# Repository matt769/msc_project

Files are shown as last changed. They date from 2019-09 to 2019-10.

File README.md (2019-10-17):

### Code
Need to run cmake/make in each of the subfolders except Microcontroller which contains Arduino/Teensyduino code files.  
FullRobot should be done last.  

Host code:  
* maps  
* path_planning  
* communication  
* FullRobot  

Microntroller code:  
* Microcontroller/Robot
* Microcontroller/IMU_calibration
* Microcontroller/Rotation

Host code dependencies:
* https://github.com/matt769/ORB_SLAM2_PRJ - clone this into same directory as this repository
* Eigen
* OpenCV
* Pangolin
* FlyCapture API (if installed in other than its default location then may need to modify FullRobot/CMakeLists.txt)

Microcontroller code dependencies (see report for links):
* PU9250
* PWMServo
* PID_v1
* Rotation (files provided, but need to be placed in stardard Arduino library location)

Other
* May need to modify include path in Robot.ino to point to communication/commPackages.h

### Supporting materials
See the Supporting_materials folder for:  
- Odroid setup instructions
- Robot build notes
- Robot development state notes *TO ADD*
- 3D/2D design files

See this link https://www.dropbox.com/sh/bz3t7idnc23njo4/AABDjr6x9dCKdW70Yl40RJT0a?dl=0 for:  
- FlyCapture API files
- Component datasheets
- Point cloud maps *TO ADD*

See this link https://github.com/matt769/2017-10_Transmitter_v2 for:
- Transmitter code

### To run
 More details on the connections are available in `build notes.pdf` if required. This is just a quick summary.

#### Using Odroid as the main computer
 * Connect Odroid and camera
 * Connect the switches and battery connectors
 * Turn them both on (Odroid circuit can be left off if just radio controlling the vehicle)
 * Connect to Odroid via ethernet cable
 * Open SSH session: IP 169.254.130.11, Username: odroid, Password: odroid
 * Run:
   * $ cd ~/ws/project/FullRobot
   * $ ./full ../../ORB_SLAM2_PRJ/Vocabulary/ORBvoc.txt PGchameleon_lowres.yaml n

#### Using an external computer
 * Connect external computer and camera
 * Connect the switch for the low level circuitry only (i.e. not the Odroid)
 * Turn it on
 * On the external computer, assuming it has the same folder structure as the Odroid (but easy to modify if not), run:
   * $ cd ~/ws/project/FullRobot
   * $ ./full ../../ORB_SLAM2_PRJ/Vocabulary/ORBvoc.txt PGchameleon_lowres.yaml y

#### Notes
The program `full` takes 3 parameters.
1. Path to Bag of Words Vocabulary file
2. Path to ORB SLAM config file (including camera intrinsic parameters) 
3. Visualisation indicator - `y` will launch the standard ORB SLAM windows to view the camera feed and map/localisation information, `n` will suppress then

In the above running instructions I have assumed visualisation disabled when using Odroid, and enabled when using an external computer.

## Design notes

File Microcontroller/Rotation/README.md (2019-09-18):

# Rotation
Library for working with 3D rotations and orientations.
Mainly written for use of quaternions. Basic Euler and and Vector objects added to support.

For Euler angles, the rotation order used is always YAW -> PITCH -> ROLL.

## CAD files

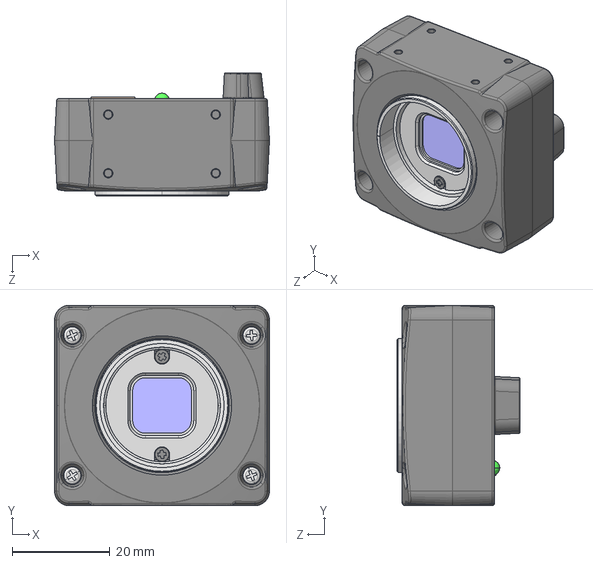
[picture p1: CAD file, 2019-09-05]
Supporting_materials/Datasheets/Camera/Drawings/Chameleon Case.STEP
44.0 x 41.0 x 25.2 mm

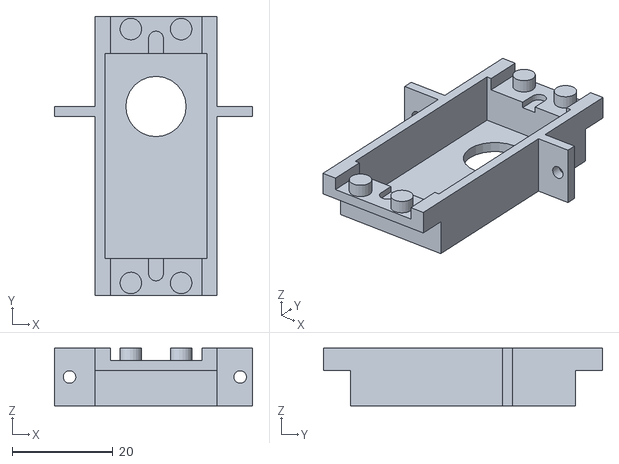
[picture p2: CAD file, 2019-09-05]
Supporting_materials/Design_files/for_3d_printing_pt2.stl
39.4 x 55.5 x 11.5

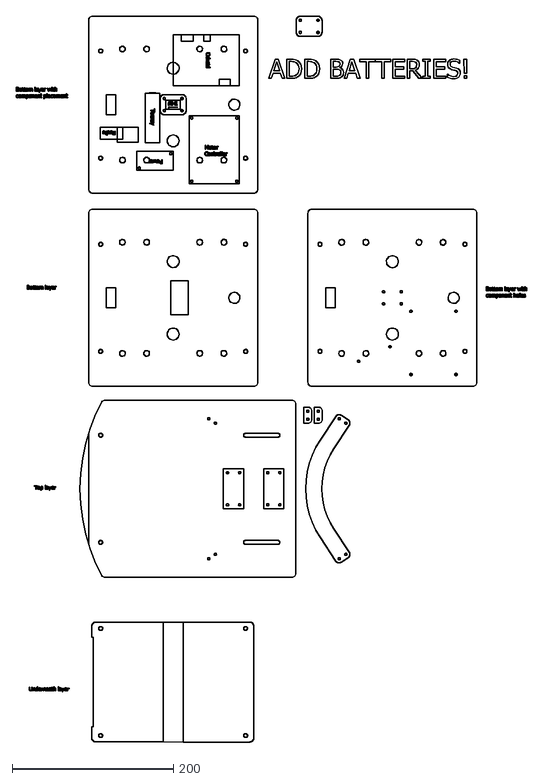
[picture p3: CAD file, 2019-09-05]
Supporting_materials/Design_files/layers_and_components.dxf
634.1 x 901.6

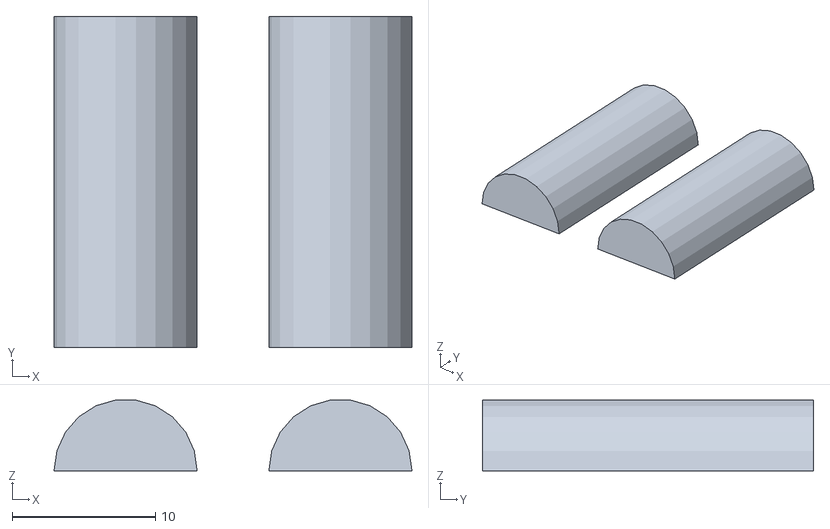
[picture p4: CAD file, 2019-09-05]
Supporting_materials/Design_files/for_3d_printing_pt4.stl
25.0 x 23.1 x 4.95

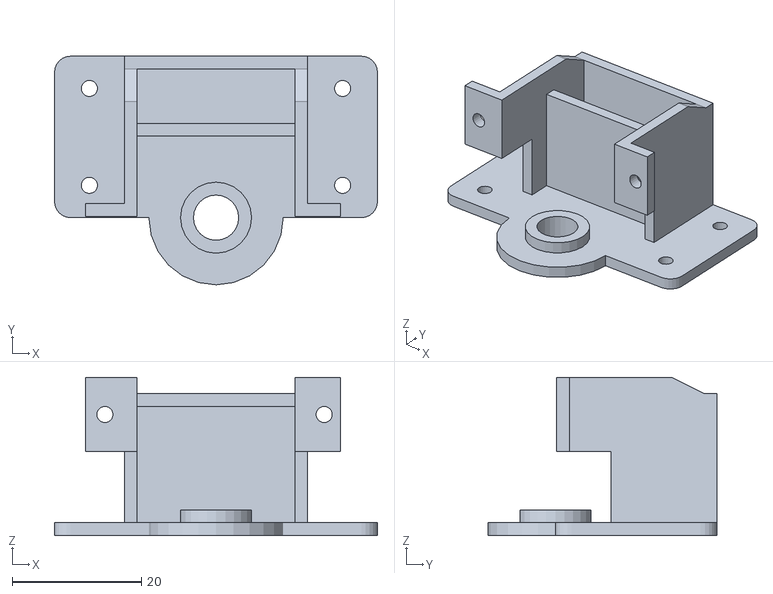
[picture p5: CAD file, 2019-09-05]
Supporting_materials/Design_files/for_3d_printing_pt1.stl
50.0 x 35.4 x 24.5

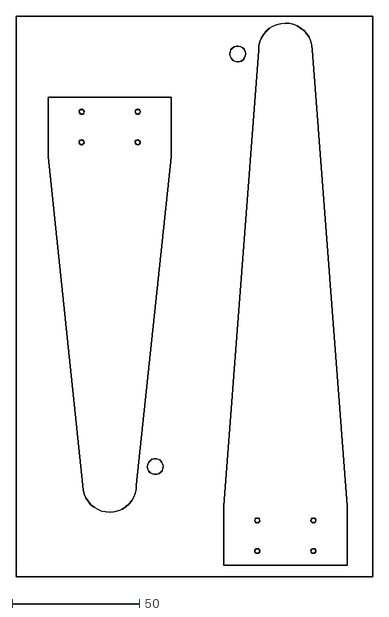
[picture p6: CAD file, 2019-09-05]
Supporting_materials/Design_files/camera_lever_for_laser_cutting.dxf
140.0 x 220.0

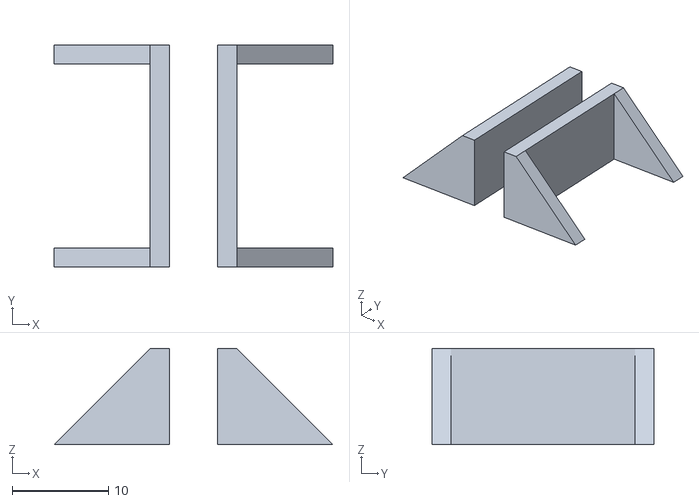
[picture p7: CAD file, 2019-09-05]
Supporting_materials/Design_files/for_3d_printing_pt3.stl
29.0 x 23.1 x 10.0

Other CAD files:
Supporting_materials/Datasheets/Camera/Drawings/Chameleon Case.x_b

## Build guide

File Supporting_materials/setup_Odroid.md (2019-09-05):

# Setting up the Odroid XU4

## Initial setup

Download Ubuntu 18.04 image for Odroid from here:  
https://wiki.odroid.com/odroid-xu4/os_images/linux/ubuntu_4.14/ubuntu_4.14  
And put on SD or eMMC card for Odroid  

Power on Odroid  
It will shut down automatically if this is the first time it's been turned on  
Turn it on again  

Now when it restarts, update linux  
$ sudo apt update  
$ sudo apt upgrade  

I received an error:  
"depmod ... module not found"  
-> according to forum this is not a problem https://forum.odroid.com/viewtopic.php?t=33481

$ sudo apt dist-upgrade
$ sudo apt autoremove
$ sudo apt install linux-image-xu3

I received an error:  
"unable to locate package"  
-> apparently not a problem, the previously dist-upgrade step should have been sufficient https://forum.odroid.com/viewtopic.php?t=31484

## Tools and dependencies
Create workspace directory  
$ mkdir ws  

### Git
$ sudo apt install git

### Eigen
$ sudo apt-get install libeigen3-dev

Note: I previously installed Eigen using the Github hosted source, but later had problems with g2o finding it

### OpenCV
$ cd ~/ws
$ sudo apt-get install cmake git libgtk2.0-dev pkg-config libavcodec-dev libavformat-dev libswscale-dev  
$ wget https://github.com/opencv/opencv/archive/3.4.2.zip  
$ unzip 3.4.2.zip  
$ cd ~/opencv  
$ mkdir build  
$ cd build  
$ cmake -D CMAKE_BUILD_TYPE=Release -D CMAKE_INSTALL_PREFIX=/usr/local ..  
$ make -j4  
$ sudo make install  

Note: I was not able to get OpenCV to install with Eigin (couldn't get it to find Eigen properly), though this is not actually required

### Pangolin
$ cd ~/ws
$ git clone https://github.com/stevenlovegrove/Pangolin.git  
$ sudo apt-get install libglew-dev  
$ cd Pangolin  
$ mkdir build  
$ cd build  
$ cmake ..  
$ cmake --build .  

### ORB_SLAM2_PRJ
$ git clone https://github.com/matt769/ORB_SLAM2_PRJ  
$ cd ORB_SLAM2_PRJ  
$ ./build.sh  

Note: The build.sh file is modified to include the -j2 argument for make when building ORB SLAM. Without this the ORB SLAM build will probably fail (on the Odroid) due to memory issues (though g2o and DBoW2 should be ok). For systems with more memory, this can be changed back to -j.

### FlyCapture
See this page:  
https://www.flir.co.uk/support-center/iis/machine-vision/application-note/getting-started-with-flycapture-2-and-arm/

I have put the file on dropbox
$ cd ~/ws
$ wget https://www.dropbox.com/s/503t7ibigvr35u0/flycapture.2.13.3.31_armhf_xenial.tar.gz?dl=0
$ mv flycapture.2.13.3.31_armhf_xenial.tar.gz?dl=0 flycapture.2.13.3.31_armhf_xenial.tar.gz
$ tar -xzf flycapture.2.13.3.31_armhf_xenial.tar.gz

$ cd flycapture.2.13.3.31_armhf/lib  
$ sudo cp libflycapture* /usr/lib  
$ sudo sh flycap2-conf  
I used user name "odroid"  
$ cd src/FlyCapture2Test  
$ make  

## Networking
Ubuntu 18.04 uses a new system (not interfaces file anymore)  

Place fillowing file 'config.yaml' (actual name doesn't matter) in /etc/netplan/  
</pre>
network:  
  version: 2  
  renderer: networkd  
  ethernets:  
    enp3s0:  
      addresses:  
        - 169.254.130.11/24  
</pre>

## Serial port permissions
This gives read/write permissions on ttyACM0  

$ sudo adduser odroid dialout  

Actually the odroid user is already a member of the dialout group. This is not the case with a standard Ubuntu install (e.g. on a laptop) I think.

## Teensy rules

Download the device rules from here https://www.pjrc.com/teensy/td_download.html
$ sudo cp 49-teensy.rules /etc/udev/rules.d/

## For normal computer
Process will be basically the same, but ensure that the correct version of the FlyCapture software is installed e.g. AMD64 for my laptop.

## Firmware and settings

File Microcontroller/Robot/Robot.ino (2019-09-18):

#include <Arduino.h>
#include <avr/io.h>
#include <avr/interrupt.h>

#include "Receiver.h"
#include "Motors.h"
#include "MPU9250.h"
#include <PWMServo.h>
#include <PID_v1.h>
#include "/home/matt/ws/project/communication/commPackages.h"
#include <Rotation.h>
#include"movingAverageFilter.h"


using namespace Comms;

uint8_t sendPackageId = 0;

// STATUS - note this is currently part of Comms, maybe should change that
Status status = Status::UNINITIALISED;
Status statusPrev = Status::UNINITIALISED;
constexpr uint8_t pinLED = 13;

MoveStatus moveStatus = MoveStatus::FINISHED;
MoveStatus moveStatusPrev = MoveStatus::FINISHED;
namespace MoveStatusDetail {
enum Enum {
  NONE,
  TURN,
  FORWARD,
  ARC
};
}
MoveStatusDetail::Enum moveStatusDetail = MoveStatusDetail::NONE;



// MODE
namespace Mode {
enum Enum {
  MANUAL,
  AUTO
};
}
Mode::Enum mode = Mode::AUTO;
Mode::Enum modePrev = Mode::AUTO;

namespace TurnDirection {
enum Enum {
  NONE,
  LEFT,
  RIGHT
};
}
TurnDirection::Enum turnDirection = TurnDirection::NONE;

namespace RobotDirection {
enum Enum {
  FORWARD,
  BACKWARD
};
}
RobotDirection::Enum robotDirection = RobotDirection::FORWARD;


// For communication with Odroid
constexpr uint8_t rxBufferSize = 32;
char rxBuffer[rxBufferSize]; // TODO review size

MovePackageRequest movePackageRequest;
PosePackageRequest posePackageRequest;
ServoPackageRequest servoPackageRequest;
StatusPackageRequest statusPackageRequest;

PackageType packageType = PackageType::EXAMPLE0;
bool newMoveRequest(false), newPoseRequest(false), newServoRequest(false), newStatusRequest(false);

constexpr uint32_t moveUpdatePeriod = 500; // how often during a movement phase that the robot will send an update to the host with distance so far



// Motors
constexpr uint8_t pinDir1 = 38;
constexpr uint8_t pinPwm1 = 37;
constexpr uint8_t pinDir2 = 36;
constexpr uint8_t pinPwm2 = 35;

Motor motorLeft(pinDir1, pinPwm1);
Motor motorRight(pinDir2, pinPwm2);
uint8_t throttleLeft;
uint8_t throttleRight;

constexpr uint8_t LOW_THROTTLE_LIMIT = 30;
constexpr uint8_t STICK_DEADZONE = 8; // on either side of centre
constexpr uint8_t STICK_CENTRE = 127;
constexpr uint8_t THROTTLE_MAX = 250;

// Servo
constexpr uint8_t pinServo = 30;
PWMServo camServo;
constexpr int servoPositionCentre = 85;
int servoPosition = servoPositionCentre; // offset + 0 // note that position is relative to centred position
constexpr int SERVO_POS_MIN = servoPositionCentre - 35; // to the left
constexpr int SERVO_POS_MAX = servoPositionCentre + 35; // to the right


// Receiver
constexpr uint8_t pinRadioCE = 25;  // RF24 enable
constexpr uint8_t pinRadioCSN = 26; // SPI Chip Select
Receiver receiver(pinRadioCE, pinRadioCSN);
uint32_t receiverLast = 0;
constexpr uint32_t receiverFreq = 50;
bool newRxData;
bool radioArmed = false;

// Encoders
constexpr uint8_t pinEncoderIntL = 18; // S1 (orange)
constexpr uint8_t pinEncoderOtherL = 17; // S2 (green)
constexpr uint8_t pinEncoderIntR = 16; // S1 (orange)
constexpr uint8_t pinEncoderOtherR = 15; // S2 (green)
volatile int32_t encCountLeft = 0;
volatile int32_t encCountRight = 0;

float trackSpeedLeft;
float trackSpeedRight;


// PIDs
// Track speeds are in millimetres per second
uint32_t lastCalculateSpeeds = 0;
constexpr uint32_t pidPeriodSpeeds = 20; // milliseconds (e.g. 20ms -> 1000/20 = 50Hz)

float leftTrackSpeedSetpoint = 0, leftTrackSpeedOutput;
float rightTrackSpeedSetpoint = 0, rightTrackSpeedOutput;
float leftKp = 0.1, leftKi = 0, leftKd = 0;
float rightKp = 0.1, rightKi = 0, rightKd = 0;

PID pidLeftTrackSpeed(&trackSpeedLeft, &leftTrackSpeedOutput, &leftTrackSpeedSetpoint, leftKp, leftKi, leftKd, PID_DIRECT);
PID pidRightTrackSpeed(&trackSpeedRight, &rightTrackSpeedOutput, &rightTrackSpeedSetpoint, rightKp, rightKi, rightKd, PID_DIRECT);



uint32_t lastCalculateHeading = 0;
constexpr uint32_t pidPeriodHeading = 100; // milliseconds

float heading = 0, requiredAngularVelocity = 0, headingSetpoint = 0;
float zeroHeading = 0;
float headingError = 0; // This will be used along with a setpoint of zero instead of the actual heading and setpoint
//  as it allows easier control of the heading wrapping
float headingKp = 2, headingKi = 0, headingKd = 0;
PID pidHeading(&headingError, &requiredAngularVelocity, &zeroHeading, headingKp, headingKi, headingKd, PID_DIRECT);




// Track movement
Vector position(0, 0, 0);


// Note, turn target is headingSetpoint so no separate variable created
float forwardTarget = 0.0;
float forwardActual = 0.0;

constexpr float headingTolerance = 5.0 * PI / 180.0;
constexpr float forwardTolerance = 5.0; // millimetres

uint32_t lastAccumulate;
constexpr uint32_t accumulatePeriod = 5;
uint32_t lastHandleMovement;
constexpr uint32_t handleMovementPeriod = 20;



// Robot measurements
constexpr int32_t driveSprocketRadius = 21;
constexpr float driveSprocketCircumference = 2.0 * PI * (float)driveSprocketRadius;
constexpr int32_t pulsesPerMotorRotation = 2;
constexpr int32_t gearRatio = 75;
constexpr float distancePerPulse = driveSprocketCircumference / (float)(pulsesPerMotorRotation * gearRatio);
constexpr float distanceBetweenTracks = 211.0;


// IMU
MPU9250 IMU(SPI1, 4);
int imuStatus;

unsigned long readImuLast = 0;
constexpr unsigned long readImuPeriod = 2; // milliseconds, e.g. 2ms = 500Hz
constexpr float readImuPeriodFloat = (float)readImuPeriod / 1000.0; // convert to seconds
Euler eulerAngles;
Quaternion orientation(1, 0, 0, 0);
float alpha = 0.01; // weight of accel in complementary filter

movingAverageFilter magXfilter;
movingAverageFilter magYfilter;
movingAverageFilter magZfilter;






// INTERRUPTS
// Because the interrutps are set to trigger on CHANGE we need to find out whether it was rising or falling
// So just read the pin again, if it's high, then it was rising
// And in one direction, both pins will be the same level, and in the other they'll be the opposite
void incrementCounterL() {
  if (digitalReadFast(pinEncoderIntL) == digitalReadFast(pinEncoderOtherL)) {
    encCountLeft += 1;
  }
  else {
    encCountLeft -= 1;
  }
}

void incrementCounterR() {
  if (digitalReadFast(pinEncoderIntR) != digitalReadFast(pinEncoderOtherR)) {
    encCountRight += 1;
  }
  else {
    encCountRight -= 1;
  }
}


// **************************************************************************************
// ************************************  SETUP  *****************************************
// **************************************************************************************

void setup() {
  //delay(2000); // required so we don't miss the first serial prints
  //while (!Serial); // This is required for the Teensy to get set up properly as a serial port on Linux
  // TODO ideally we should be able to start up with just the radio

  statusPrev = status;
  status = Status::INITIALISING;
  pinMode(pinLED, OUTPUT);
  digitalWrite(pinLED, HIGH);

  // Radio alternative SPI pins
  SPI.setSCK(27);

  // IMU alternative SPI pins
  SPI1.setSCK(20);
  SPI1.setMISO(5);
  SPI1.setMOSI(21);

  // Radio setup
  receiver.setup(); // TODO add check and halt program like IMU if required
  receiver.setAckBattery(7); // report full battery (to stop controller battery light flashing a lot)

  // if there's no serial connection but we do have radio input, then continue
  while ((!Serial) && (!receiver.checkForNewData())) {
    delay(100);
  }


  // Encoder setup
  setupEncoders();

  // IMU setup
  imuStatus = IMU.begin();
  if (imuStatus < 0) {
    Serial.println("IMU initialization unsuccessful");
    Serial.println("Check IMU wiring or try cycling power");
    Serial.print("Status: ");
    Serial.println(imuStatus);
    while (1) {} // TODO change to set status and error flags
  }

  // Specific settings
  // Some of these are already the default but for clarity I put them here anyway
  IMU.setAccelRange(MPU9250::ACCEL_RANGE_2G);
  IMU.setGyroRange(MPU9250::GYRO_RANGE_250DPS);
  IMU.setDlpfBandwidth(MPU9250::DLPF_BANDWIDTH_20HZ);
  // There aren't really any options available for Mag
  // Except read rate which is already set to 100Hz within IMU.begin()

  // calibration info
  IMU.setAccelCalX(0.2534242, 0.9977166);
  IMU.setAccelCalY(0.2825031, 0.9991337);
  IMU.setAccelCalZ(0.5199513, 0.9813061);

  IMU.setMagCalX(52.7316322, 0.8228859);
  IMU.setMagCalY(-36.4627380, 1.1055350);
  IMU.setMagCalZ(-24.8827744, 1.1360730);

  // initialise magmetometer filters
  initialiseMagFilters();
  // use accel and mag to get initial orientation
  calculateInitialOrientation();



  // Servo setup
  camServo.write(servoPosition);
  camServo.attach(pinServo);
  camServo.write(servoPosition);

  // wait for the expected radio input (throttle down-up-dowm) and then start main program
  //  receiver.armingProcedure();/
  motorLeft.setDir(MotorDirection::FORWARD);
  motorRight.setDir(MotorDirection::FORWARD);

  // PIDs
  pidLeftTrackSpeed.SetSampleTime(pidPeriodSpeeds);
  pidRightTrackSpeed.SetSampleTime(pidPeriodSpeeds);
  pidLeftTrackSpeed.SetOutputLimits(-30, 30);   // PWM
  pidRightTrackSpeed.SetOutputLimits(-30, 30);   // PWM
  pidLeftTrackSpeed.SetMode(PID_AUTOMATIC); // TODO after testing this should be removed - PID should only be on when a movement is being made
  pidRightTrackSpeed.SetMode(PID_AUTOMATIC); // TODO after testing this should be removed - PID should only be on when a movement is being made

  pidHeading.SetSampleTime(pidPeriodHeading);
  pidHeading.SetOutputLimits(-1, 1);  // Radians
  pidHeading.SetMode(PID_AUTOMATIC);


  // initialise all timing variables
  uint32_t timeNow = millis();
  lastCalculateSpeeds = timeNow;
  lastAccumulate = timeNow;
  lastHandleMovement = timeNow;
  readImuLast = timeNow;


  statusPrev = status;
  status = Status::READY;

  digitalWrite(pinLED, LOW);
  Serial.println(F("Starting..."));

  // FOR TESTING
  //  statusPrev = status;
  //  status = Status::ACTIVE;
}


// **************************************************************************************
// ************************************  LOOP  ******************************************
// **************************************************************************************

void loop() {

  receiveRequests();
  processStatusRequest(); // ALWAYS respond to status request

  // TODO handle status changes

  if (status == Status::ACTIVE) {
    processMoveRequest();
    processPoseRequest();
    processServoRequest();
  }

  // note that it doesn't matter what kind of status the robot is in
  // can always take manual control by turning the radio on
  // at the moment, no way to go back to auto
  if (millis() - receiverLast >= receiverFreq) {
    receiverLast += receiverFreq;
    newRxData = receiver.checkForNewData();
    if (newRxData) {
      //Serial.println("Radio data received");
      if (mode != Mode::MANUAL) {
        modePrev = mode;
        mode = Mode::MANUAL;
      }
      if (status != Status::UNDER_MANUAL_CONTROL) {
        statusPrev = status;
        status = Status::UNDER_MANUAL_CONTROL;
      }
    }
  }

  // TODO handle mode changes

  if ((mode == Mode::MANUAL) && (!receiver.checkHeartbeat())) {
    statusPrev = status;
    status = Status::SHUTDOWN;
  }

  handleStatusChanges();


  if ((mode == Mode::MANUAL) && newRxData) {
    // Why is this not in the checkForNewData() bit?
    // because I want to make it clearer where the mode change is
    if (radioArmed) {
      processRadioInput();
    }
    else {
      radioArmed = receiver.armingProcedure();
    }
    newRxData = false;
  }



  if (status != Status::SHUTDOWN) {

    if (millis() - lastAccumulate > accumulatePeriod) {
      accumulateMovement();
      lastAccumulate += accumulatePeriod;
    }

    // TODO move actual move functions out of handleMovement()
    //   then handleMovement can run every loop
    // and the move functions can be run periodically
    if (millis() - lastHandleMovement > handleMovementPeriod) {
      handleMovement();
      lastHandleMovement += handleMovementPeriod;
    }

    if (millis() - lastCalculateSpeeds > pidPeriodSpeeds) {
      if (moveStatus == MoveStatus::MOVING) {
        calculateTrackSpeeds();
        pidLeftTrackSpeed.Compute();
        pidRightTrackSpeed.Compute();
        // update motors
        // TODO add methods to motors to handle this stuff?
        updateMotorsWithPidOutputs();

        // TODO note that if taking the speed down to 0, it will get there before PWM is zero
        // will need to handle this properly
      }
      lastCalculateSpeeds += pidPeriodSpeeds;
    }


    if (millis() - readImuLast > readImuPeriod) {
      IMU.readSensor(true, true, true); // read accels and gyros and mags
      // only update filters if readings have changed
      // if move read to separate lower frequency loop, may be no need for this
      float mx = IMU.getMagX_uT();
      float my = IMU.getMagY_uT();
      float mz = IMU.getMagZ_uT();

      if (mx != magXfilter.latest() ||
          my != magYfilter.latest() ||
          mz != magZfilter.latest()) {
        magXfilter.update(mx);
        magYfilter.update(my);
        magZfilter.update(mz);
        calculateYaw(magXfilter.output, magYfilter.output, magZfilter.output); // not actually using the result from this at the moment
      }

      gyroUpdate(IMU.getGyroX_rads(), IMU.getGyroY_rads(), IMU.getGyroZ_rads(), readImuPeriodFloat);
      accelUpdate(IMU.getAccelX_mss(), IMU.getAccelY_mss(), IMU.getAccelZ_mss(), alpha);

      readImuLast += readImuPeriod;
    }

    // TEST IMU
    static unsigned long lastPrintImu = 0;
    if (millis() - lastPrintImu > 1000) {
      //Euler currentAngles(orientation);
      //printEuler(currentAngles, 1, true);
      //Serial.println(orientation.getYaw());
      lastPrintImu += 1000;
    }

  }

} // Loop




// **************************************************************************************
// ******************************  SETUP FUNCTIONS  *************************************
// **************************************************************************************


void setupEncoders() {
  pinMode(pinEncoderIntL, INPUT);
  pinMode(pinEncoderOtherL, INPUT);
  pinMode(pinEncoderIntR, INPUT);
  pinMode(pinEncoderOtherR, INPUT);
  attachInterrupt(digitalPinToInterrupt(pinEncoderIntL), incrementCounterL, CHANGE);
  attachInterrupt(digitalPinToInterrupt(pinEncoderIntR), incrementCounterR, CHANGE);
}


// **************************************************************************************
// ****************************  RECEIVE SERIAL DATA  ***********************************
// **************************************************************************************

// If a whole package is available (and it should be given the way data is transmitted over USB)
//  then this function will block until the whole package is processed
// If there are multiple then the next package will be processed the next time this function is called
void receiveRequests() {
  static uint8_t c;
  static uint8_t idx = 0;
  static bool receivingPackage = false;
  static bool receiptComplete = false;
  //  static bool parseComplete = false; // Think I can remove this
  static uint8_t packageId;
  //static uint8_t packageIdPrev;
  while ((Serial.available() > 0) && !receiptComplete) {
    c = Serial.read();
    digitalWrite(pinLED, LOW);
    if (c == '<') {
      receivingPackage = true;
      idx = 0;
      //      Serial.print("Start\n");
    }
    else if (c == '>') {
      // only want to flag as complete if previously received a start marker
      if (receivingPackage) {
        receivingPackage = false;
        receiptComplete = true;
        rxBuffer[idx] = '\0';
        //        Serial.print("Stop\n");
      }
    }

    else if (receivingPackage) {
      // handle too large packages just in case
      if (idx >= rxBufferSize) {
        // stop receiving and wait for new start marker
        receivingPackage = false;
      }
      else {
        rxBuffer[idx] = c;
        idx++;
      }
    }
  }

  if (receiptComplete) {
    //    Serial.println(rxBuffer);

    char *val = strtok(rxBuffer, "\t");
    if (val != nullptr) {
      packageType = static_cast<PackageType>(atoi(val));
      //      Serial.println(packageType);
    }
    else {
      Serial.println("Package type problem");
      receiptComplete = false;
      return;
    }

    val = strtok(nullptr, "\t");
    if (val != nullptr) {
      packageId = atoi(val);
      //      Serial.println(packageId);
    }

    // add check on package id?

    switch (packageType) {

      case PackageType::MOVE:
        val = strtok(nullptr, "\t");
        movePackageRequest.moveType = static_cast<MoveType>(atoi(val));
        val = strtok(nullptr, "\t");
        movePackageRequest.turn = atof(val);
        val = strtok(nullptr, "\t"); // Does it not matter that there isn't a \t following the final value ??
        movePackageRequest.forward = atof(val);
        //        Serial.println(movePackageRequest.moveType);
        //        Serial.println(movePackageRequest.turn);
        //        Serial.println(movePackageRequest.forward);
        newMoveRequest = true;
        break;

      case PackageType::POSE:
        // This request has no associated data
        newPoseRequest = true;
        break;

      case PackageType::SERVO:
        val = strtok(nullptr, "\t");
        servoPackageRequest.angle = atoi(val);
        newServoRequest = true;
        break;

      case PackageType::STATUS:
        val = strtok(nullptr, "\t");
        statusPackageRequest.requestedStatus = static_cast<Status>(atoi(val));
        newStatusRequest = true;
        break;

      default:
        Serial.println("Unrecognised package type");
        break;
    }
    receiptComplete = false;
  }
}


// **************************************************************************************
// ****************************  RECEIVE RADIO DATA  ************************************
// **************************************************************************************

// TODO decouple receipt and motor setting
//  // RECEIVER AND MOTORS
//  // Should the motors actually be updated here? Or decouple setting pwm/direction from actual update and do that in separate bit?
//  // Would need to save motor directions as well
void processRadioInput() {
  //      receiver.printPackage();

  // Not using this mode yet
  //      if (receiver.getControlBit(3) == 0) {
  //        mode = Mode::MANUAL;
  //      }
  //      else {
  //        mode = Mode::AUTO;
  //      }

  if (receiver.getControlBit(2) == 0) {
    robotDirection = RobotDirection::FORWARD;
  }
  else {
    robotDirection = RobotDirection::BACKWARD;
  }

  uint8_t throttle = receiver.getThrottle();
  if (abs(throttle) <= LOW_THROTTLE_LIMIT) {
    throttle = 0;
  }
  int16_t yawDifferential = (int16_t)receiver.getYaw() - STICK_CENTRE;
  if (abs(yawDifferential) <= STICK_DEADZONE) {
    yawDifferential = 0;
    turnDirection = TurnDirection::NONE;
  }
  if (yawDifferential < 0) {
    turnDirection = TurnDirection::LEFT;
  }
  else if (yawDifferential > 0) {
    turnDirection = TurnDirection::RIGHT;
  }
  float yawDifferentialPC = abs((float)yawDifferential) / (float)STICK_CENTRE;

  // TURN
  if (throttle > 0) {
    if (robotDirection == RobotDirection::FORWARD) {
      motorLeft.setDir(MotorDirection::FORWARD);
      motorRight.setDir(MotorDirection::FORWARD);
    }
    else if (robotDirection == RobotDirection::BACKWARD) {
      motorLeft.setDir(MotorDirection::BACKWARD);
      motorRight.setDir(MotorDirection::BACKWARD);
    }
    if (turnDirection == TurnDirection::NONE) {
      throttleLeft = throttle;
      throttleRight = throttle;
    }
    else if (turnDirection == TurnDirection::LEFT) {
      throttleLeft = (uint8_t)(min((float)throttle * (1.0 - yawDifferentialPC), 255.0));
      throttleRight = (uint8_t)(min((float)throttle * (1.0 + yawDifferentialPC), 255.0));
    }
    else if (turnDirection == TurnDirection::RIGHT) {
      throttleLeft = (uint8_t)(min((float)throttle * (1.0 + yawDifferentialPC), 255.0));
      throttleRight = (uint8_t)(min((float)throttle * (1.0 - yawDifferentialPC), 255.0));
    }
  }

  // PIVOT
  else if (throttle == 0 && yawDifferential != 0) {
    if (turnDirection == TurnDirection::LEFT) {
      motorLeft.setDir(MotorDirection::BACKWARD);
      motorRight.setDir(MotorDirection::FORWARD);
    }
    else if (turnDirection == TurnDirection::RIGHT) {
      motorLeft.setDir(MotorDirection::FORWARD);
      motorRight.setDir(MotorDirection::BACKWARD);
    }
    uint8_t pivotThrottle = (uint8_t)((float)THROTTLE_MAX * yawDifferentialPC);
    throttleLeft = pivotThrottle;
    throttleRight = pivotThrottle;
  }
  else {
    throttleLeft = 0;
    throttleRight = 0;
  }

  if (throttleLeft < LOW_THROTTLE_LIMIT) throttleLeft = 0;
  if (throttleRight < LOW_THROTTLE_LIMIT) throttleRight = 0;
  motorLeft.setPwmValue(throttleLeft);
  motorRight.setPwmValue(throttleRight);

  // And let the roll (right stick left/right) control the servo
  uint8_t servoInput = receiver.getRoll();
  servoPosition = map(servoInput, 0, 255, 60, 120);
  camServo.write(servoPosition);
}




// **************************************************************************************
// *******************************  SEND PACKAGES  **************************************
// **************************************************************************************


void sendMovePackage() {
  Serial.print(startByte);
  Serial.print(static_cast<int>(PackageType::MOVE));
  Serial.print(delim);
  Serial.print(sendPackageId);
  Serial.print(delim);
  Serial.print(static_cast<int>(moveStatus));
  Serial.print(delim);
  Serial.print(position.x);
  Serial.print(delim);
  Serial.print(position.y);
  Serial.print(delim);
  Serial.print(position.z);
  Serial.print(endByte);
  Serial.print('\n'); // not required - just for ease of viewing if doing so directly
  Serial.send_now();
  sendPackageId++;
}
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

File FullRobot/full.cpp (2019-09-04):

#include <stdio.h>

#include "FlyCapture2.h"
#include <unistd.h>

#include<iostream>
#include<chrono>

#include<opencv2/core/core.hpp>
#include <Eigen/Dense>


#include<System.h>
#include<Converter.h>
#include <atomic>

#include "communications.h"
#include "commPackages.h"
#include "camera.h"
#include "GridMap.h"
#include "astar.h"
#include "transformations.h"


// Declare supporting functions (definitions are at the bottom of the file)
bool setOrCheckRobotStatus(const Comms::Status &newOrExpectedStatus, const std::chrono::seconds &timeoutPeriod);
bool setRobotStatus(const Comms::Status &newStatus, const std::chrono::seconds &timeoutPeriod);
bool checkRobotStatus(const Comms::Status &expectedStatus, const std::chrono::seconds &timeoutPeriod);
bool servoSweep();
bool servoMove();
bool mapExtractionAndAnalysis(ORB_SLAM2::System& SLAM, const Eigen::RowVector3f robotPos,
                              const float scale, const float stepSize, const float mapLimit,
                              Eigen::MatrixXf& mapPoints, GridMap& map);
Eigen::Matrix<float,4,4> toMatrix4f(const cv::Mat &cvMat4);
void calculateRequiredMovement(const Eigen::Matrix<float, 4, 4>& robotPose,
                          const Eigen::Vector2f& targetPos,
                          Eigen::Vector2f& requiredMovements);
void outputMap(std::string fileName, const Eigen::MatrixXf& mapPcd);



int main(int argc, char **argv) {
    // ***************************************************************
    // ********************* SETUP ***********************************
    // ***************************************************************
    std::cout << "Starting...\n";

    // Check input args ok
    if (argc != 4) {
        cerr << endl << "Usage: ./mono_tum path_to_vocabulary path_to_settings use_viewer(y/n)" << endl;
        return 1;
    }

    bool useViewer = true;
    if (*argv[3] == 'n') {
        useViewer = false;
    }


    // Parameters
    constexpr float stepSize = 100.0; // 10mm, the footprint of the robot is made up of roughly 25 squares of this size
    constexpr float mapLimit = 1000.0; // 1m





    // Utility variables
    bool resBool; // for checking return values
    int resInt; // for checking return values

    // Robot state variables
//    Comms::Status robotState = Comms::Status::UNINITIALISED; // reflects state of microcontroller, not this program
    int servoAngleDeg = 0; // TODO this isn't used everywhere yet e.g. servo sweep function
                            //   should be master state of servo (always up to date)



    // Timer variables, we'll use this to control anything that requires timing e.g. servo sweep, map analysis
    auto examplePeriod = std::chrono::milliseconds(100);
    std::chrono::time_point<std::chrono::steady_clock> tStart;
    std::chrono::time_point<std::chrono::steady_clock> tEnd;
    std::chrono::time_point<std::chrono::steady_clock> tNow;
//    bool response = false;
//    bool timeout = false;
    auto timeoutPeriod = std::chrono::seconds(3);
    bool ok;

    // Start listening for messages from the robot
    std::cout << "Set up receiver\n";
    Comms::setup();
    // TODO consider changing to
    //  std::thread receiveThread(&Comms::receiveInBackground);
    //  because I'm not sure I need the pointer
//    std::thread *receiveThreadPointer;
//    receiveThreadPointer = new std::thread(&Comms::receiveInBackground);
    std::thread commThread(&Comms::receiveInBackground);
    usleep(1000);

    // Check robot status is READY
    std::cout << "Check robot status\n";
    ok = checkRobotStatus(Comms::Status::READY, std::chrono::seconds(10));
    if (!ok) {
        std::cout << "Exiting program\n";
        return 1;
    }

    std::cout << "Setting robot status to active\n";
    ok = setRobotStatus(Comms::Status::ACTIVE, std::chrono::seconds(3));
    if (!ok) {
        std::cout << "Exiting program\n";
        return 1;
    }

    // initialise camera
    // includes all required settings for this application
    // TODO check return value and exit if required
    FlyCapture2::setup();


    // initialise SLAM
    ORB_SLAM2::System SLAM(argv[1], argv[2], ORB_SLAM2::System::MONOCULAR, useViewer);
    ORB_SLAM2::Tracking* trk = SLAM.getTracking();



    // necessary variables for image capture flow
    FlyCapture2::Image rawImage;
    FlyCapture2::Image convertedImage;
    cv::Mat cvImage;
    FlyCapture2::Error error;

    // PLACEHOLDER - acquire image
    resInt = FlyCapture2::acquire(rawImage, convertedImage, cvImage);
    if (resInt > 0) {
        std::cout << "Error in image capture - need to handle better probably\n";
        std::cout << "Exiting program\n";
        return 1;
    }
    // run SLAM tracking
    // What format is this timestamp supposed to be??
    // I think it's seconds (based on the example sequences)
    std::chrono::duration<float> tFrame;
    tStart = std::chrono::steady_clock::now();
    tFrame = tStart - tStart;
    SLAM.TrackMonocular(cvImage, tFrame.count());




    // ***************************************************************
    // ************* TRY TO INITIALISE ORBSLAM MAP *******************
    // ***************************************************************

    // is there really much advantage to having wrapped stuff ni servoSweep() ?

    const int maxSweeps = 3;
    for (int sweepNo = 0; sweepNo < maxSweeps; sweepNo++) {

        // servoSweep will return false until it completes
        while (!servoSweep()) {

            // acquire image
            resInt = FlyCapture2::acquire(rawImage, convertedImage, cvImage);
            if (resInt > 0) {
                std::cout << "Error in image capture - need to handle better probably\n";
                std::cout << "Exiting program\n";
                return 1;
            }

            // PLACEHOLDER - give SLAM the current estimated pose TO BE CONFIRMED

            // run SLAM tracking
            tNow = std::chrono::steady_clock::now();
            tFrame = tNow - tStart;
            SLAM.TrackMonocular(cvImage, tFrame.count());

        }

        std::cout << "Sweep " << sweepNo + 1 << "\n";
        if (SLAM.GetTrackingState() == ORB_SLAM2::Tracking::eTrackingState::OK) {
            std::cout << "SLAM map initialised, ending sweep phase\n";
            break;
        }
    }


    // check SLAM state and if not initialised, end program
    if (SLAM.GetTrackingState() != ORB_SLAM2::Tracking::eTrackingState::OK) {
        std::cout << "ORB SLAM not initialised\n";
        std::cout << "Exiting program\n";
    }


    // ***************************************************************
    // ************************ GET SCALE ****************************
    // ***************************************************************

    // TODO should check after each step if tracking lost and go back to last known good point if so
    //  and stay there for a few cycles
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

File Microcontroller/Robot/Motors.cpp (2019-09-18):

// NOTE - I DON'T THINK FLIPPING OF DIRECTION WORKS PROPERLY

#include "Motors.h"

// Should I handle pin modes here as well?

Motor::Motor(const uint8_t pinDir, const uint8_t pinPwm): pinDir(pinDir), pinPwm(pinPwm) {
  //state = MotorState::OFF;
  init();
};

Motor::Motor(const uint8_t pinDir, const uint8_t pinPwm, bool reverse): pinDir(pinDir), pinPwm(pinPwm) {
  //state = MotorState::OFF;
  init();
  flipDir = reverse;
};


void Motor::init() {
  pwmValue = 0;
  pwmValuePrev = 0;
  direction = MotorDirection::FORWARD;
  directionPrev = MotorDirection::BACKWARD; // just to force a write in update function()
  pinMode(pinDir, OUTPUT);
  pinMode(pinPwm, OUTPUT);
  update();
}

MotorState::Enum Motor::getState() {
  if (pwmValue != 0) {
    return MotorState::ON;
  }
  else {
    return MotorState::OFF;
  }
}

MotorDirection::Enum Motor::getDirection() {
  return direction;
}

uint8_t Motor::getPwmValue() {
  return pwmValue;
}

void Motor::setPwmValue(uint8_t newPwm) {
  pwmValue = newPwm;
  update();
}

void Motor::setDir(MotorDirection::Enum newDir){
  direction = newDir;
  update();
}

void Motor::setDirAndPwmValue(MotorDirection::Enum newDir, uint8_t newPwm) {
  // add control of forward/backward transition?
  setDir(newDir);
  setPwmValue(newPwm);
}

//void Motor::setState(MotorState::Enum newState) {
//  state = newState;
//}


void Motor::setDirAndPwmValue(int16_t signedPwm){
  MotorDirection::Enum newDir;
  if(signedPwm >= 0){
    newDir = MotorDirection::FORWARD;
  }
  else if (signedPwm < 0){
    newDir = MotorDirection::BACKWARD;
  }
  uint16_t newPwm = abs(signedPwm);
  newPwm = constrain(newPwm, 0, 255);
  
  setDirAndPwmValue(newDir, (uint8_t)newPwm);
}

//void Motor::adjustSpeed(int16_t signedPwmChange){
//  // TODO remove this - it doesn't really make sense since it can't handle direction correctly
//  // with the way the class operates at the moment
//}



void Motor::update() {
  if (pwmValue != pwmValuePrev) {
    analogWrite(pinPwm, pwmValue);
  }
  
  if (direction != directionPrev) {
    uint8_t directionMod;
    if (flipDir) {
      directionMod = 1 - (uint8_t)direction;
    }
    else {
      directionMod = (uint8_t)direction;
    }
    digitalWriteFast(pinDir, directionMod);
  }
  
  pwmValuePrev = pwmValue;
  directionPrev = direction;
  //  statePrev = state;
}

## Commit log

2019-09-05 Added supporting materials.
    [Chameleon Case.STEP, Chameleon Case.x_b, camera_lever_for_laser_cutting.dxf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]
2019-09-18 Removed submodules so missing files now correctly included.
    [Motors.cpp, Receiver.cpp, Robot.ino]
